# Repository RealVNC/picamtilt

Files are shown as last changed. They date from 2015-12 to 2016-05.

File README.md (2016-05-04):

# picamtilt

A UI for controlling a pan-tilt unit with a mounted Raspberry Pi camera, 
overlayed with the camera preview image.

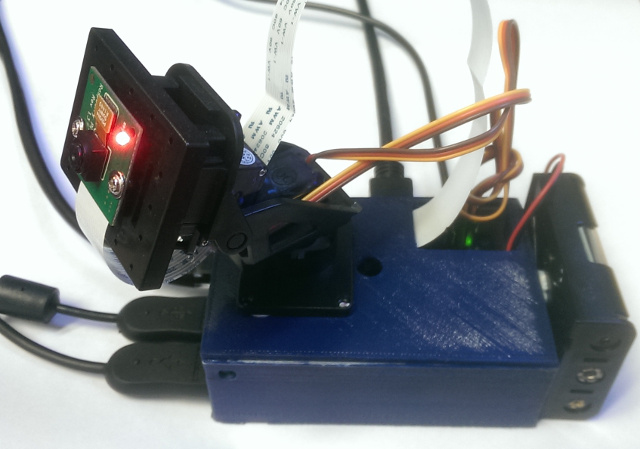
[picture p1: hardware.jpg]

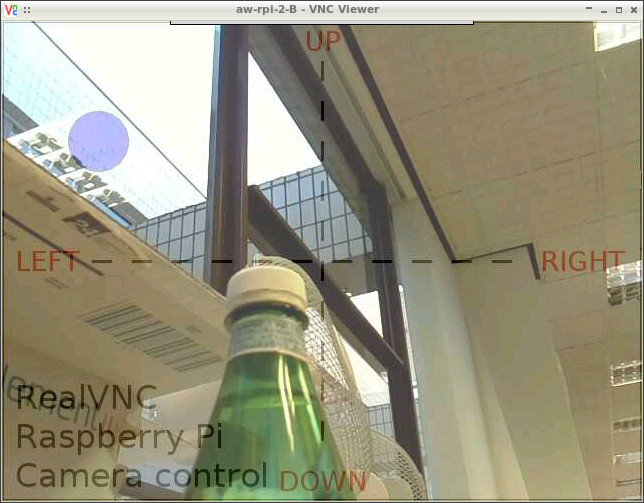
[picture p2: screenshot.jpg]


Written in Python, using Tkinter for the UI and the picamera Python module
to control the Raspberry Pi camera preview.

Run the program from the repo directory, via sudo:
```bash
$ sudo python picamtilt.py
```

The program creates a full-screen window, with cross-hairs and a blue circle 
showing the current camera position. The Raspberry Pi camera preview is shown 
full-screen with transparency, so the UI is superimposed on the camera image.

Controls are:
- Mouse click: moves the camera to specific point.
- Arrow keys: Moves the camera by fixed amount in that direction.
- Space: Move to the centre.
- d: Enters "demo mode", where the camera will move about randomly (any other key exits demo).
- q: Quits the program.

This was written to provide a demonstration of RealVNC's
[VNC Server for Raspberry Pi](https://www.realvnc.com/products/vnc/raspberrypi/) 
at the [PiWars](http://piwars.org/) event in December 2015.

**Update [2016-05-04]**: There is now an [Alpha version of VNC Server](https://github.com/RealVNC/raspi-preview) available for the Raspberry Pi which allows you to view the entire display output, including the GPU overlays used by the camera preview and Minecraft. You will need this version in order to view the camera image remotely.

---

The following instructions detail how to build the complete system:

## Hardware

### Parts required

- Official Raspberry Pi camera 
You could also use the PI NOIR camera if you want to do infra-red.

- [Pan+tilt unit](http://4tronix.co.uk/store/index.php?rt=product/product&keyword=tilt&category_id=0&product_id=435) with servos and camera mount, from 4tronix

- Long camera cable (30cm or more)
The standard cable supplied with the Raspberry Pi camera is too short when used
with the Pan+tilt unit.

- [PWM/servo hat](http://www.adafruit.com/products/2327) for Raspberry Pi, from Adafruit

- A Raspberry Pi
Any model except the Pi Zero (since it has no camera connector), but preferably 
one of the newer models (2B, B+ or A+) which are designed to fit HAT add-ons. 
According to Adafruit, the PWM hat can be made to fit onto an older Pi if longer 
headers are used.

- A suitable power supply for the Raspberry Pi.

- A suitable power supply for the servos (see powering the servos section).

### Assembly

Assemble everything, remembering to thread the camera cable through the slot in
the PWM hat and plugging this into the Pi before attaching the hat. Observe the
polarity of the servo connections (brown wire=gnd, red=+v, orange=signal), and 
plug the cable from the pan (rotate) servo into channel 0 and the tilt (up/down) 
servo into channel 1. Note that the hat can support a total of 16 servos, so 
there is plenty of room for adding extra functionality!

### Powering the servos

You should also use a separate power supply for the servos, since it is not 
recommended to power them off the same supply as the Pi. This [3 AA battery box](http://www.maplin.co.uk/p/3-aa-battery-box-yr61r) from Maplin is suitable.
Plus a [PP3 battery clip connector](http://www.maplin.co.uk/p/pp3-snap-battery-clip-hf28f), 
which can be wired to the screw terminals on the PWM hat (also observing the 
polarity!). Using standard alkaline AA batteries, this provides a 4.5v supply
to the servos.

### Case

A suitable case was 3D printed to house the Raspberry Pi and PWM hat, and 
allow the Pan+tilt unit to be mounted on top. The following case was used from
Thingiverse:
[Raspberry Pi B+ Case with Camera Hole "Valkyrie" by rgbextruder](http://www.thingiverse.com/thing:552193)

The top was modified by cutting out a hole in the corner to allow access to the
PWM outputs, and to allow the camera and power cables to enter. The STL file 
for the modified top is included in this repo as "case_top_cutout.stl", and is
licensed under the [Creative Commons - Attribution - Share Alike license](http://creativecommons.org/licenses/by-sa/3.0/)

## Software

- Install the python package for controlling the Pi camera
```bash
$ sudo apt-get install python-picamera
```

- Install the python Tkinter UI library: 
```bash
$ sudo apt-get install python-tk
```

- Follow the [Adafruit tutorial](https://learn.adafruit.com/adafruit-16-channel-pwm-servo-hat-for-raspberry-pi/) 
to setup the PWM hat and install the software.

- Clone this repo and copy in the required files from the Adafruit-Raspberry-Pi-Python-Code
installation directory, e.g. (assuming you installed it under your home directory):
```bash
$ git clone https://github.com/RealVNC/picamtilt.git
$ cd picamtilt
$ cp ~/Adafruit-Raspberry-Pi-Python-Code/Adafruit_PWM_Servo_Driver/Adafruit_PWM_Servo_Driver.* .
$ cp ~/Adafruit-Raspberry-Pi-Python-Code/Adafruit_I2C/Adafruit_I2C.* .
```

- Install the [Alpha version of VNC Server](https://github.com/RealVNC/raspi-preview) for Raspberry Pi, following the instructions to have it start on boot. This will allow you to view and control the camera remotely using a VNC Viewer (available for [desktop platforms](http://www.realvnc.com/download/viewer/) as well as [iOS](http://www.realvnc.com/products/ios/), [Android](http://www.realvnc.com/products/android/) and [Chrome](http://www.realvnc.com/products/chrome/)).

Copyright (C) 2015 RealVNC Limited. All rights reserved.

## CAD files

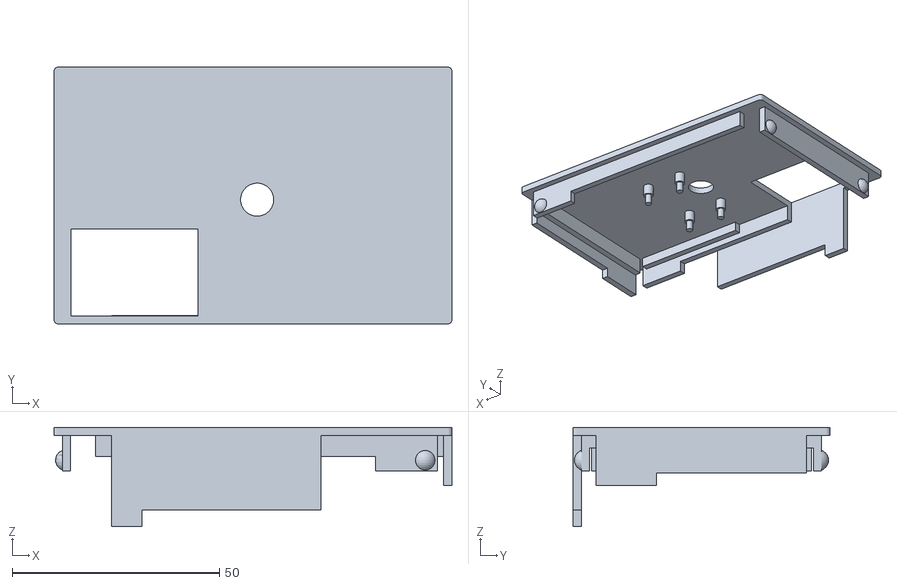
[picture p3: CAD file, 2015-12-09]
case_top_cutout.stl
96.0 x 62.0 x 24.0
